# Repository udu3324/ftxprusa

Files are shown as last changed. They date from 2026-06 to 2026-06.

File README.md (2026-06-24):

# ftxprusa

A fusion of the Folger Tech FT-6 and Prusa MK3S+

ftxprusa

 * FT-6 Frame
 * FT-6 Kinematics/linear rails
 * FT-6 Heatbed
 * FT-6 Bed Thermistor
 * FT-6 Power supply
 * MK3S+ Extruder module
 * MK3S+ Einsy Rambo mainboard controller
 * MK3S+ Stepper motors
 * MK3S+ Screen display
 * Raspberry Pi Zero 2 W running MainsailOS

## Why

I want to turn garbage into something useful again. Folger Tech is a discontinued brand of 3d printers and is obsolete today. There are a bunch of leftover Prusa MK3S+ parts from upgraded MK4s. Why not put these both together and create something amazing?

|  | 
|:--:| 
| Pressure advance test |

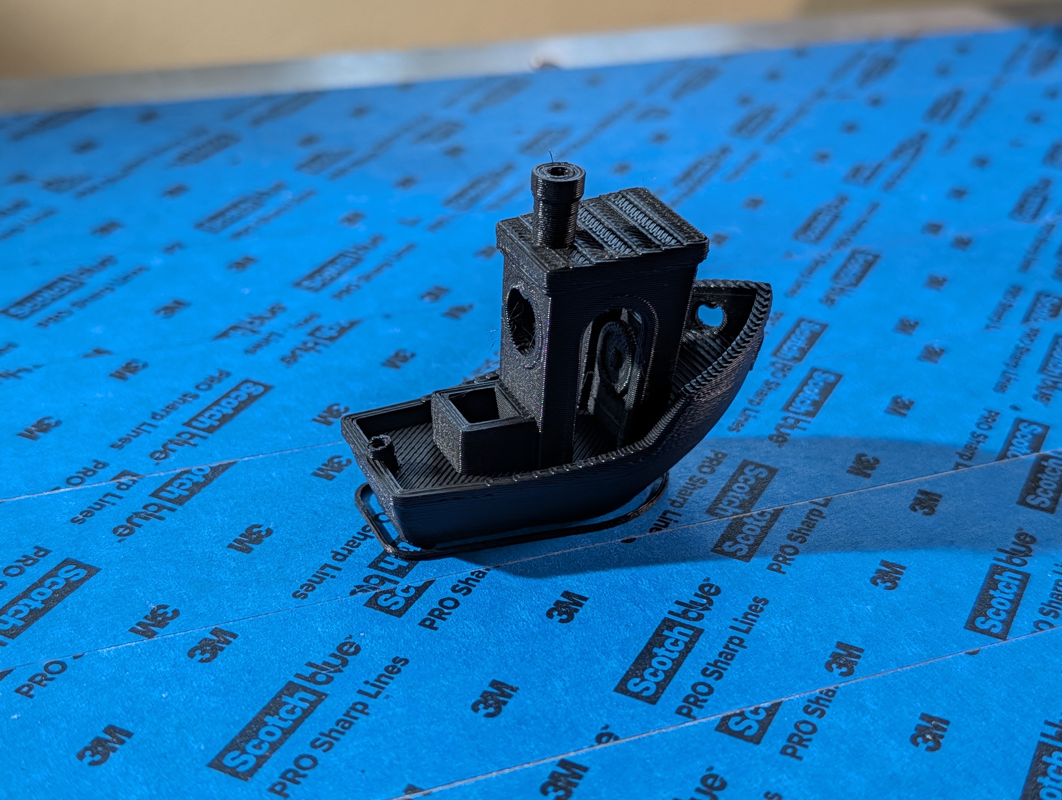
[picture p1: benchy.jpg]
|  | 
|:--:| 
| Finished Benchy on ftxprusa |

|  | 
|:--:| 
| Benchy in progress |

|  | 
|:--:| 
| Prusa MK3S+ display on FT-6 frame with swapped electronics |

## How to Build

The build process below is more of a rough outline and is very unpolished. Please proceed with caution and plan accordingly before doing anything!

Note: I unfortunately do not have the cad for the mount between the y-axis linear sled and mk3s+ extruder module.

1. Scrap all of the FT-6's electronics and leave behind anything mechanical. This includes removing its original control boards, stepper motors, wires, and more. (don't remove the pcb contacting the y-axis stepper, just the stepper itself) NOTE: Keep the FT-6's heatbed and heatbed electronics, including the ac converter to it.
2. Take apart two MK3S+ z-axis stepper motors and swap the leadscrews with the FT-6's leadscrews. CAUTION: This is a super invasive process and requires epoxy. Make sure to keep any bite marks on the FT-6 leadscrews in the stepper motor. If you have more plain Prusa stepper motors, I suggest using those instead with shaft couplers. 
3. Install the MK3S+ extruder onto the rail sled
4. Drill a 30mm diameter hole into the aluminum composite sheet that holds the two x-axis motors. This will allow routing more wires through to the control box.
5. Install the Einsy Rambo into the electronics box, as well as a switch between the ac plug to power supply to allow turning off the printer
6. Install the MK3S+ Screen display
7. Connect all neccesary cables, with any extension or custom crimped cables if needed (you definitely do need them)
8. Install MainsailOS onto your RPI Zero 2 W and install the config files provided in this repository, as well as config files for your slicer
9. Fix the USB DFU firmware issue prone on Einsy Rambo boards [here](https://github.com/PrusaOwners/mk3-32u2-firmware)
10. Add masking/painters tape to the aluminum bed to allow better first layer adhesion
11. Done! You now have a giant printer that works half way and needs some more tinkering before its perfect

## Calibration

Start with these things roughly in order to calibrate. The config in this repository is set to my values which may not work universally

1. Calibrate your bed flatness (z-offset, bed screws, etc.)
2. PID tune your bed and nozzle heater
3. Make sure you have the right [idler screw tension](https://help.prusa3d.com/article/idler-screw-tension_177367)
4. Calculate your right "steps per mm" for your extruder [here](https://ellis3dp.com/Print-Tuning-Guide/articles/extruder_calibration.html)
5. Calculate your [pressure advance value](https://ellis3dp.com/Print-Tuning-Guide/articles/index_pressure_advance.html) (i included the gcode i've generated in /gcode)

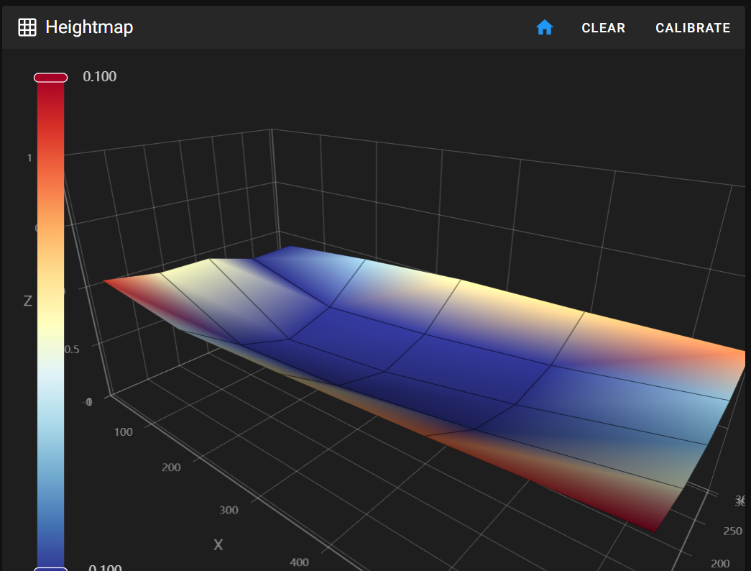
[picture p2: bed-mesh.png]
bed mesh
|  | 
|:--:| 
| Calibrated bed mesh with PINDA and bed heated to 60C |

## Problems Encountered

The factory bed of the ft-6 is incredibly bent and warped. The bed mesh heightmap calibration allows the z-axis to dynamically adjust itself to how warped it is.

The x-axis linear rails had to be shifted a bit to the left to allow more usage of the bed and extend its width

Tilt on the x-axis is super common due to both leadscrews of the z axis not synced together with a belt, in addition to the bed being heavy and automatically lowering due to gravity and no power

The z-axis is a little wonky and not consistent in its z movement, causing z-calibration to be really hard (the bed is susceptible to vibration due to too high of velocity/accel. on the z-axis)

## Results

In the end, I was able to make a solid quality 3d printer after ~5 days of tuning. (not including modding/build time, possibly a month max or so) 
There are still some strange power problems and z-axis calibration still being annoying, but everything else is flawless while printing. 

I would 100% daily drive this printer.

## Sources

 * https://github.com/charminULTRA/Klipper-Input-Shaping-MK3S-Upgrade
 * The above was a huge help in configuring the mk3s parts for its firmware
 * https://www.printables.com/model/155387-0017-remix-x2-delta-p-duct-v2r22-for-the-mk3s-new
 * I upgraded to this better overhang fan duct, It may not be neccesary but I recommend it. Note: The config files does not account for the extra space that is leftover and unused

## Huge Thanks to

 * MainsailOS and klipper for existing (marlin took very long to reflash/compile changes)
 * My robotics instructor for donating this printer to further tinker around
 * The 3d printing community for the vast amount of resources and documentation to make this possible

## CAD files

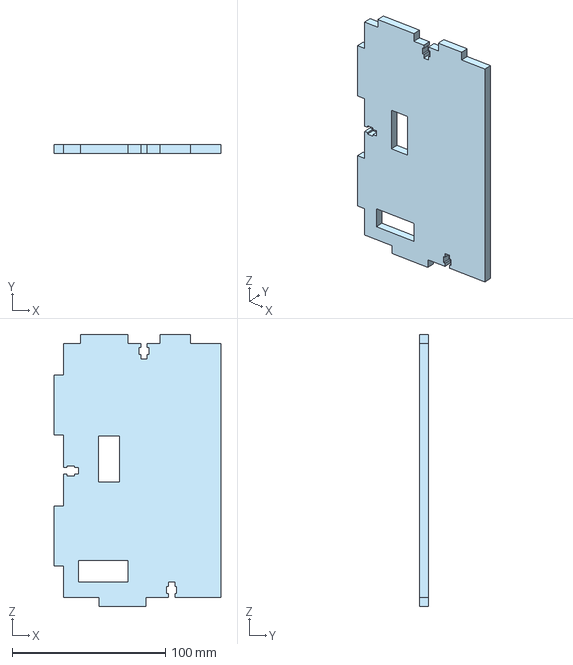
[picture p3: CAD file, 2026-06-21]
cad/side electrical box plate.step
108.6 x 6.00 x 177.2 mm

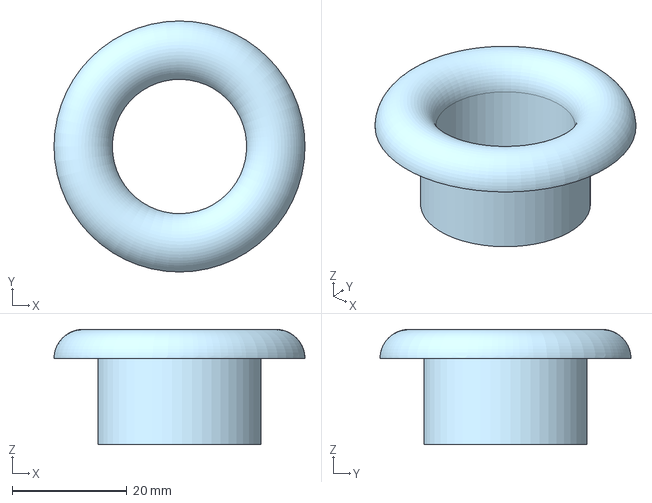
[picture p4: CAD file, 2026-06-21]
cad/cable saver.step
43.7 x 43.7 x 20.1 mm

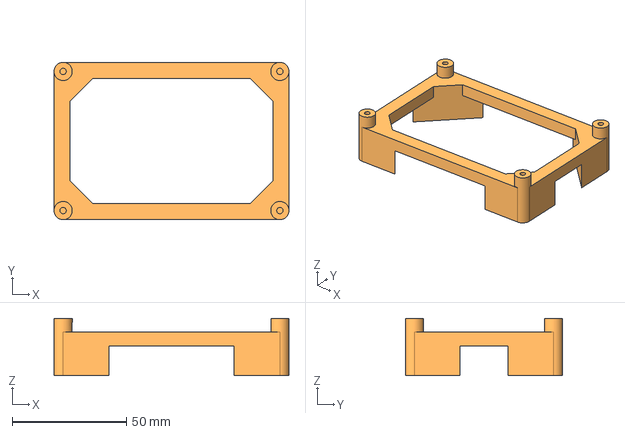
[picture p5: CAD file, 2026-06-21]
cad/einsy rambo electronics box mount.step
103.0 x 69.0 x 25.0 mm

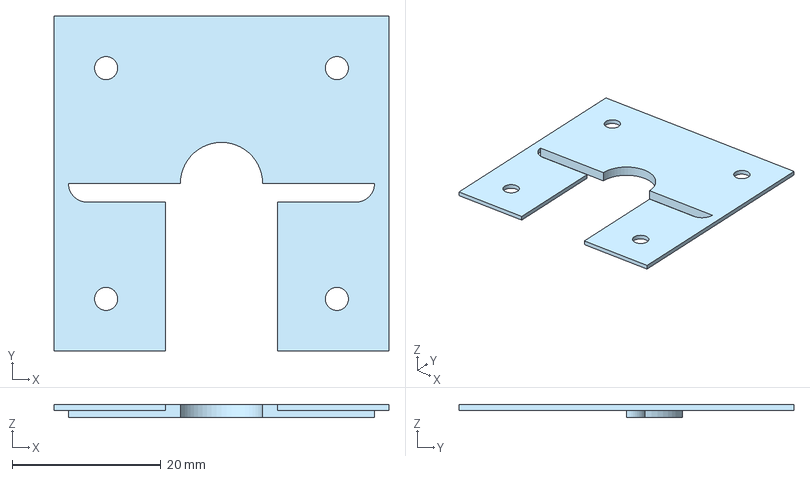
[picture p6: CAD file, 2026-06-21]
cad/stepper motor z axis drill guide.step
45.0 x 45.0 x 1.80 mm

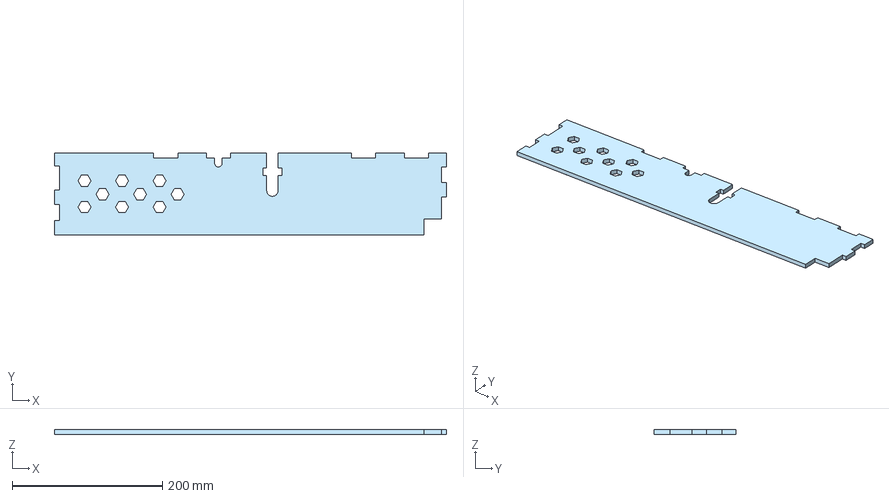
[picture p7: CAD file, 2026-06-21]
cad/top electrical box plate.step
522.3 x 108.8 x 6.00 mm

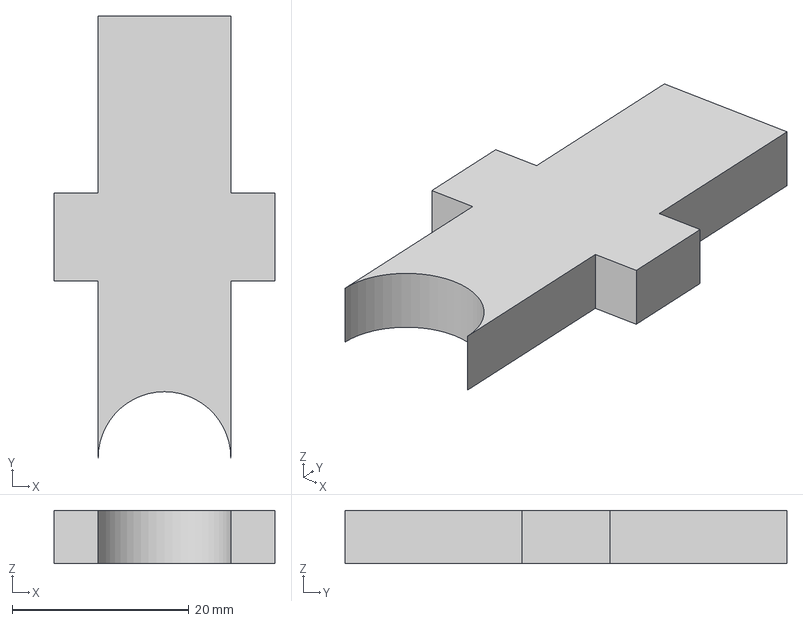
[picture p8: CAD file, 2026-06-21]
cad/top electrical box cable holder.step
25.0 x 50.0 x 6.00 mm

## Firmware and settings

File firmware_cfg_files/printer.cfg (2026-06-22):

#####           CharminULTRA Prusa MK3S+ Klipper Config Template

##### ***********REVIEW THE README INSTRUCTIONS FOR ALL STEPS***************

# Uncomment the necessary items as you walk through this file. Many are already uncommented. Look for TUNE ME for important areas to tune to your specific printer.
# TUNING STEPS ARE NOT OPTIONAL.

### UI and Built-in Macros (see macros.cfg for added macros)
[include mainsail.cfg]

### PRINTER - Machine Limits are set inside of Klipper rather than from PrusaSlicer
[printer]
kinematics: cartesian

## MK3.5 Settings based on MK3.5 IS PrusaSlicer factory profile machine limits
max_velocity: 300
max_accel: 4000
minimum_cruise_ratio: 0.5
max_z_velocity: 6 # halved due to bed vibration messing up bed mesh probe accuracy
max_z_accel: 375  # ^

## MK3S+ Settings based on MK3S+ PrusaSlicer factory profile machine limits, if you want to maintain stock speed limits for some reason.
#max_velocity: 200
#max_accel: 1000
#minimum_cruise_ratio: 0.5
#max_z_velocity: 12
#max_z_accel: 200

## Z-OFFSET 
## Copy this from your current setting on Prusa, but make it absolute (removing -). You WILL need to still calibrate this properly, 
## as the probe algorithms between Prusa and Klipper firmware are slightly different.
## Note: Different Z-Offsets for different bed sheets is not yet implemented, but editing this file is a fairly simple method. You can only enable ONE at a time.
[probe]
#z_offset = 0.000 #Regular bed sheet
#z_offset = 0.000 #PETG on regular bed sheet, add/delete/edit as needed
#z_offset = 0.000 #Satin bed sheet, add/delete/edit as needed
#z_offset = 0.000 #Textured bed sheet, add/delete/edit as needed
#z_offset = 0.000 #Smooth bed sheet, add/delete/edit as needed

[mcu]
serial: /dev/ttyACM0 # If you are using RPI via USB connection to printer
#serial: /dev/serial0 # If you are using internal RPI serial port, not recommended.
restart_method: command

### CONTROL BOARD
[include einsy-rambo.cfg]

### BASE SETUP
[include display.cfg]
[include steppers.cfg]
[include tmc2130.cfg]



### HOTEND, BED and EXTRUDER - 

## Possible Hotends - This config file is intended for stock Prusa components. If you are using a non-stock hotend or extruder, please see the example configuration files in the dz0ny repository, upon which this project is based. These are not guarunteed to be correct, but a good start.
## 1) Stock V6
## 2) Dragon Standard Flow
## 3) Rapido
## 4) Revo
## 5) Other hotends are easily configurable, but do not have existing pre-made config code.

##Possible Extruders: If you are using a non-stock extruder, please see the example configuration files in the dz0ny repository, upon which this project is based. Changing extruders can require significant modification to your overall configuration, and will require your own research/work.
## 1) Stock Prusa
## 2) BMG 
## 3) Sherpa 8T and 10T
## 4) Other extruders are configurable, but do not have existing pre-made config code.

[extruder]
##TUNE ME
##Extruder Rotation Distance - Prior to calibration, make sure your Idler Screw Tension is correct: https://help.prusa3d.com/article/idler-screw-tension_177367
rotation_distance: 22.500620 #Make sure you tune this for your individual machine: https://ellis3dp.com/Print-Tuning-Guide/articles/extruder_calibration.html

##TUNE ME
##Items below come from performing PID Tuning, yours will be unique!!
#control = pid
#pid_kp = 29.944
#pid_ki = 2.037
#pid_kd = 110.045


##TUNE ME
##Pressuer Advance Section - Perform this tuning for your individual machine: https://ellis3dp.com/Print-Tuning-Guide/articles/index_pressure_advance.html
##ENTER THE PA VALUE VALUE IN SLICER FILAMENT SETTINGS - In Filament Settings Custom G Code section (allows you to print with different PA for each filament, more flexibile than here).
##You may also enter a set a global value here if you want, but it's not recommended.
pressure_advance: 0.04

nozzle_diameter: 0.4 # Remember to change this if you change nozzle diameter.
min_extrude_temp: 170
min_temp: 0
max_temp: 285
full_steps_per_rotation: 200
filament_diameter: 1.750
max_extrude_only_distance: 200
max_extrude_cross_section: 50.0
max_extrude_only_velocity: 120.0
max_extrude_only_accel: 1250.0 #Limited to the retraction accel on the MK3.5

[heater_bed]
##TUNE ME
##Items below come from performing PID Tuning, yours will be unique!! 
#control = pid
#pid_kp = 48.658
#pid_ki = 0.603
#pid_kd = 981.685




### MACROS
[include macros.cfg]

[pause_resume]

[include pause.cfg]


### INPUT SHAPING

# Uncomment ONE of the two lines below, depending on which accelerometer board you are using.
#[include adxlmcu-KUSBA.cfg] # ONLY FOR USE DURING INPUT SHAPING TESTING - Leaving this on without the accelerometer plugged in will cause Klipper to not work.
#[include adxlmcu-BTT.cfg] # ONLY FOR USE DURING INPUT SHAPING TESTING - Leaving this on without the accelerometer plugged in will cause Klipper to not work.

[input_shaper]


### OTHER FEATURES OR TUNING
[exclude_object]

### SKEW CORRECTION - This is the LAST tuning procedure. Follow instructions.
##TUNE ME
[skew_correction]

### THIRD PARTY FEATURES

### MISC
[menu __main __octoprint]
type: disabled #Removes Octoprint from physical printer menu. Not needed.

[safe_z_home]
home_xy_position: 11,6
speed: 50.0
z_hop: 15
z_hop_speed: 15.0
move_to_previous: False



###
### STOP
###
### Do not edit anything below this line. The printer will store values here automatically when you
###  perform the SAVE_CONFIG command. They may look like they are commented out but any line that
###  starts with #*# will be read in by Klipper and applied.
###
### When you are done with the guide you should see sections below for extruder, heater_bed, probe, and input_shaper.
###
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

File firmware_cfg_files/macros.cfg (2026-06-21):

# WARNING: DO NOT EDIT THIS FILE UNLESS YOU KNOW WHAT YOU ARE DOING

#Start of Charmin's additions:

# Print Start
[gcode_macro PRINT_START]
gcode:
    {% set BED_TEMP = params.BED_TEMP|default(60)|float %}
    {% set BED_CAL_TEMP = params.BED_CAL_TEMP|default(60)|float %}
    {% set EXTRUDER_TEMP = params.EXTRUDER_TEMP|default(215)|float %}
    {% set EXTRUDER_CAL_TEMP = params.EXTRUDER_CAL_TEMP|default(170)|int %} ; 170*C gets common filaments like PETG, PLA, and ASA/ABS nice and soft without oozing.
    {% set PRINTER_MODEL = params.PRINTER_MODEL|default("MK3S+")|string %}
    {% set FILAMENT_TYPE = params.FILAMENT_TYPE|default("PLA")|string %}

    ; Make sure the MK3S+ uses the bed temp as the calibration temp since SuperPINDA has internal compensation
    {% if PRINTER_MODEL == "MK3S+" %}
        {% set BED_CAL_TEMP = BED_TEMP %}
    {% endif %}

    ; using TEMPERATURE_WAIT instead of M109/M190 speeds up the startup time by minutes. Klipper seems to wait
    ; with very little hysteresis and especially with the bed, this can take a long time.

    M117 Preheating...
    M140 S{BED_CAL_TEMP}             ; Start bed heating and don't wait
    M104 S{EXTRUDER_CAL_TEMP}        ; Start heating extruder and don't wait. Saves time later between bed mesh calibration and purge.
    SET_GCODE_OFFSET Z=0.0           ; Reset the G-Code Z offset
    BED_MESH_CLEAR                   ; Clear bed mesh
    G28                              ; Home the printer
    G90                              ; Absolute positioning mode
    G0 Z50 F4000                     ; Raise up a bit for any nozzle cleaning while the bed heats (and keep PINDA cool)
    TEMPERATURE_WAIT SENSOR=heater_bed MINIMUM={BED_CAL_TEMP-1} MAXIMUM={BED_CAL_TEMP+3}
    TEMPERATURE_WAIT SENSOR=extruder MINIMUM={EXTRUDER_CAL_TEMP-1} MAXIMUM={EXTRUDER_CAL_TEMP+5}
    {% if PRINTER_MODEL == 'MK3S' or PRINTER_MODEL == "MK3" %}
        ; This is a poor way of utilizing PINDA. Normally one would want to calibrate it and store those values.
        ; Prusa implements calibration of temp vs offset and storage/retrival of those values in EEPROM.
        ; So for a lack of that, just always do bed mesh at the same temp.
        G0 X20 Y60 Z0.15             ; Move to pinda preheat position (based on calibration position in MK3/3S firmware)
        {% for timer in range(45,0,-1) %}
            M117 PINDA Heatsoak...{timer|int}
            G4 P1000
        {% endfor %}
    {% endif %}
    M117 Probing bed...
    BED_MESH_CALIBRATE ADAPTIVE=1    ; Measure bed mesh
    M117 Heating...
    M140 S{BED_TEMP}                 ; Start heating bed to final temp and don't wait 
    M104 S{EXTRUDER_TEMP}            ; Start heating extruder to final temp and don't wait
    G0 X0 Y-4 Z15 F4000              ; move to the purge starting position
    TEMPERATURE_WAIT SENSOR=heater_bed MINIMUM={BED_TEMP-1} MAXIMUM={BED_TEMP+3}
    TEMPERATURE_WAIT SENSOR=extruder MINIMUM={EXTRUDER_TEMP-1} MAXIMUM={EXTRUDER_TEMP+5}
    M117                             ; Clear message on LCD
    PRUSA_LINE_PURGE                 ; Purge and then ready to go
    #LINE_PURGE                      ; You can use this instead of PRUSA_LINE_PURGE if you install KAMP 
    #SKEW_PROFILE LOAD=CaliFlower


# Print End
[gcode_macro PRINT_END]
gcode:
    #SET_SKEW CLEAR=1
    M83 ; extruder relative mode
    G1 E-4 ; retract filament a bit for minimizing ooze
    _TOOLHEAD_PARK_PAUSE_CANCEL    ; Park
    G90 ; absolute positioning
    G0 Z{[printer.toolhead.position.z, 50]|max} F300 ; park at least 50mm off the bed
    M84 X Y E    ; Disable steppers
    TURN_OFF_HEATERS    ; Disable heaters
    M106 S0     ; Disable fans
    BED_MESH_CLEAR    ; Clear bed mesh




[gcode_macro PRUSA_LINE_PURGE]
## Purge line macro based on the MK4
gcode:
    SAVE_GCODE_STATE NAME=prusa_line_purge
    M83 ; extruder relative mode
    G0 X0 Y-4 Z15 F4000; move to the purge starting position
    G92 E0 ; reset extruder position
    G1 E3 ; prime hotend
    G0 E7 X15 Z0.2 F500 ; purge
    G0 X25 E4 F500 ; purge
    G0 X35 E4 F650 ; purge
    G0 X45 E4 F800 ; purge
    G0 X48 Z0.05 F8000 ; wipe, move close to the bed
    G0 X51 Z0.2 F8000 ; wipe, move quickly away from the bed
    RESTORE_GCODE_STATE NAME=prusa_line_purge
    G92 E0 ; reset extruder position



[force_move]
enable_force_move: true ; enable FORCE_MOVE and SET_KINEMATIC_POSITION



## Macros below obtained from origina dz0ny repository

[gcode_macro M486]
gcode:
    CLEAR_PAUSE

[gcode_macro G80]
gcode:
    M117 Bed leveling
    BED_MESH_CALIBRATE
    G1 X0 Y0 Z0.4 F4000
    M117
    M400

[gcode_macro G81]
gcode:
 BED_MESH_OUTPUT
 
[gcode_macro M300]
gcode:
    # Use a default 1kHz tone if S is omitted.
    {% set S = params.S|default(1000)|int %}
    # Use a 10ms duration is P is omitted.
    {% set P = params.P|default(100)|int %}
    SET_PIN PIN=BEEPER_pin VALUE=0.5 CYCLE_TIME={ 1.0/S if S > 0 else 1 }
    G4 P{P}
    SET_PIN PIN=BEEPER_pin VALUE=0
    
[gcode_macro UNLOAD_FILAMENT]
gcode:
  # Default ram distance and sequence copied from MK3.5 in https://github.com/prusa3d/Prusa-Firmware-Buddy/include/marlin/Configuration_MK3.5_adv.h
  {% set RAM_DISTANCE = params.RAM_DISTANCE|default(20)|int %}
  SAVE_GCODE_STATE NAME=unload_state
  G91
  {% if params.TEMP is defined or printer.extruder.can_extrude|lower == 'false' %}
    M117 Heating...
    # Heat up hotend to provided temp or 220 as default as that should work OK with most filaments.
    M109 S{params.TEMP|default(220, true)}
  {% endif %}
  SET_FILAMENT_SENSOR SENSOR=fsensor ENABLE=0
  M117 Unloading filament...
  G92 E0.0                      ; reset extruder distance
  G91                           ; relative positioning
  G1 E{RAM_DISTANCE} F1500      ; ram to build up pressure
  G1 E-50 F2700                 ; fast, long retract to thin the whisp
  G1 E-5 F50                    ; slow retract to break the whisp
  G1 E-50 F1500                 ; move filament past gears
  G92 E0.0                      ; reset extruder distance
  M400                          ; wait for planner to flush
  M117 Remove Filament Now!
  M300 S300 P1000               ; beep
  M117 Filament unloaded!
  RESTORE_GCODE_STATE NAME=unload_state
  SET_FILAMENT_SENSOR SENSOR=fsensor ENABLE=1

[gcode_macro LOAD_FILAMENT]
gcode:
  SAVE_GCODE_STATE NAME=load_state
  G91
  # Heat up hotend to provided temp or 220 as default as that should work OK with most filaments.
  {% if params.TEMP is defined or printer.extruder.can_extrude|lower == 'false' %}
  M117 Heating...
  M109 S{params.TEMP|default(220, true)}
  {% endif %}
  SET_FILAMENT_SENSOR SENSOR=fsensor ENABLE=0
  M117 Loading filament...
  # Load the filament into the hotend area.
  G92 E0.0
  G91
  G1 E70 F400
  G1 E40 F100
  G90
  G92 E0.0
  M400
  M117 Filament loaded!
  SET_FILAMENT_SENSOR SENSOR=fsensor ENABLE=1
  RESTORE_GCODE_STATE NAME=load_state

[delayed_gcode clear_display]
initial_duration: 0.
gcode:
  M117



# Prusa's calibrate Z
[gcode_macro Calibrate_Z]
description: Calibrate Z axis
gcode:
    {% set max_z = printer.toolhead.axis_maximum.z|float %}
    {% if printer.toolhead.homed_axes != "xyz" %}
      G28
    {% endif %}
    G1 X20 Y0
    G1 Z{max_z-10} F2000 #Update with Z height.
    FORCE_MOVE STEPPER=stepper_z Distance=20 Velocity=10
    G1 Z{max_z-50} F2000 # Move down
    G28 # Home again

[gcode_macro PREHEAT_PLA]
gcode:
    # Start bed heating
    M140 S60
    # Start nozzle heating
    M104 S200

[gcode_macro PREHEAT_PETG]
gcode:
    # Start bed heating
    M140 S90
    # Start nozzle heating
    M104 S240

[gcode_macro PREHEAT_TPU]
gcode:
    # Start bed heating
    M140 S50
    # Start nozzle heating
    M104 S190

# Color change or filament runout
[gcode_macro M600]
description: Color change or filament runout
gcode:
    # Default to the middle front of the bed. MK4 likes the right side but with the MK3 you might need access
    #  to the idler to unjam filament during a runout. 
    #
    # No Z specified here since PAUSE hands over to _TOOLHEAD_PARK_PAUSE_CANCEL which doesn't take a Z argument.
    # If you want to change the amount of Z lift for parking, change the value of 'custom_park_dz' in mainsail.cfg.
    #
    # If a manual Z move is done, its not possible to know the restore context since this is generally followed
    #  by an asynchronous filament load and resume.
    {% set X = params.X|default(printer.toolhead.axis_maximum.x / 2)|float %}
    {% set Y = params.Y|default(-4)|float %}
    PAUSE X={X} Y={Y}
    UNLOAD_FILAMENT RAM_DISTANCE=7 ; reuse the unload routine so we don't have to maintain two implementations
    M117 Swap filament now

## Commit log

2026-06-21 add media and info
    [side electrical box plate.step]
2026-06-22 add bed mesh result
2026-06-22 fix z-motor speed while doing bed mesh
    [einsy-rambo.cfg, printer.cfg]
